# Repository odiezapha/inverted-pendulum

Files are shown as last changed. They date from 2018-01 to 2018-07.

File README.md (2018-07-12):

# Reaction Wheel Stabilized Inverted Pendulum
An inverted pendulum that maintains an upright attitude via reaction wheels. This repository
contains hardware and software development files. See the pdf for system equations.

Renderings:<br />
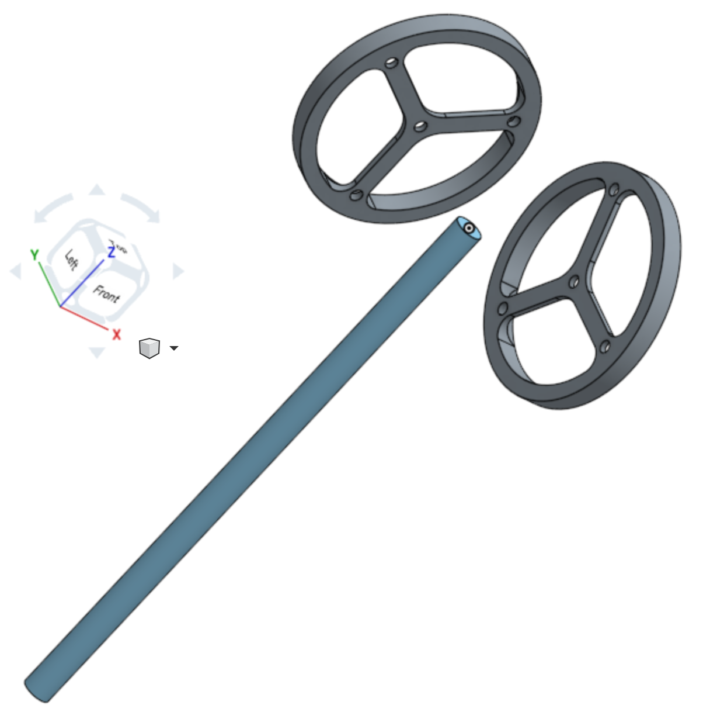
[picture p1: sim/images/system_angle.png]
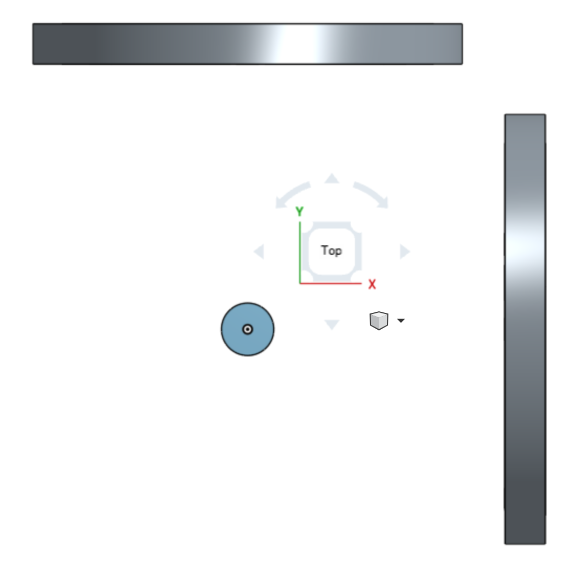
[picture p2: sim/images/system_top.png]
 

Simulation output:<br />
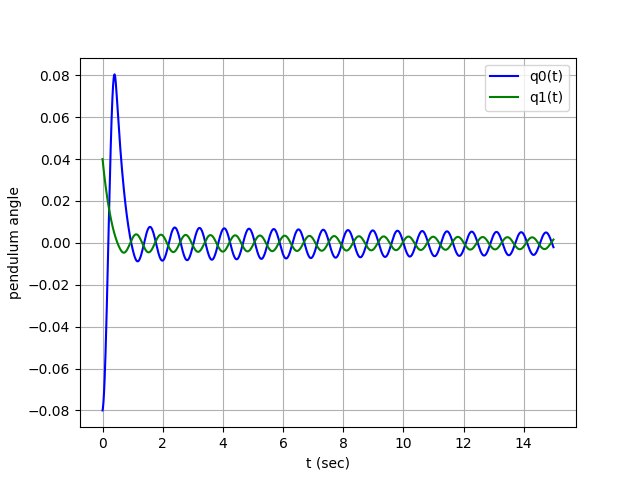
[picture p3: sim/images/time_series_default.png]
<br />
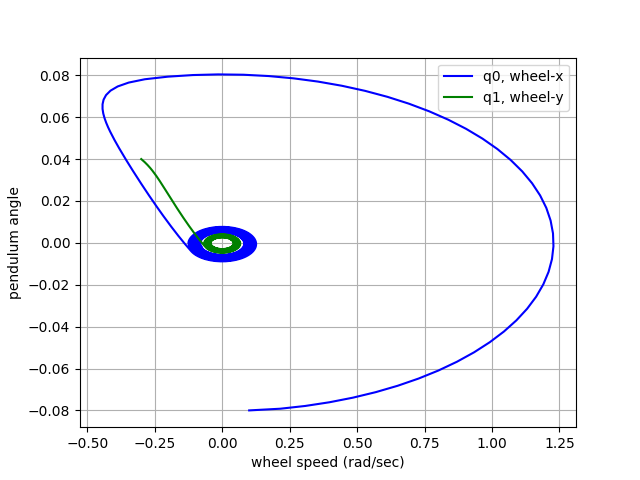
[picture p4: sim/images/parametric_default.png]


**Sim Test Conditions**<br />
Software: Python 3.6.4 on macOS High Sierra<br />
Computer: MacBook (Retina, 12-inch, Early 2015)<br />
Processor: 1.1 GHz Intel Core M<br />
RAM: 8 GB 1600 MHz DDR3<br />

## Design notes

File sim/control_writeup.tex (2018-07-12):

\documentclass{article}
\setlength{\parskip}{1em}
\usepackage{amsmath}
\usepackage{listings}
\usepackage{graphicx}
\graphicspath{ {./images/} }
\allowdisplaybreaks

\begin{document}

\centerline{\sc \large Reaction Wheel Stabilized Inverted Pendulum}
\vspace{.25pc}
\centerline{\sc \small optimal control, state space, and quaternions, oh my}
\vspace{.5pc}
\centerline{\sc Trent Fehl}
\vspace{1pc}

\begin{abstract}
In an attempt to develop some new skills, I started development of an 
inverted pendulum. This paper describes the system and the optimal 
controller development for the reaction wheel stabilized inverted pendulum.
Not included in this paper is the printed circuit board design, part 
selection, CAD models for the wheels, and machine paths for wheel manufacture.
I drew from papers concerning optimal control of a cart stabilized inverted 
pendulum, PID control of a reaction wheel stabilized inverted pendulum, 
and finally satellite control systems papers that utilize quaternions.
\end{abstract}

\section*{System Description}
\noindent This inverted pendulum is stabilized by the spinning of reaction wheels
mounted to the end of the pendulum. Only the case of a pendulum which is 
initiated and is controlled to its inverted position is being considered.
In addition to the wheels at the end of the pendulum rod, there is mass
associated with motors, a printed circuit board, batteries, and structure.
Theses are not shown in the image below but their masses are configurable 
variables for the control system.

\begin{figure}[h]
\centering
\begin{minipage}{.5\textwidth}
 \centering
 
 \caption{System rotated.}
\end{minipage}%
\begin{minipage}{.5\textwidth}
 \centering
 
 \caption{Top of system.}
\end{minipage}
\end{figure}

\noindent The equations of motion were determined and are described below.
These equations are used to build a state space representation
of the system. The state space representation takes the form 
$\boldsymbol{\dot{x}(t)} = \boldsymbol{A}\boldsymbol{x(t)} + 
\boldsymbol{B}\boldsymbol{u(t)}$ where $x(t)$ is the system state 
at time $t$, $u(t)$ is the input to the system at time $t$, and $A$ 
and $B$ are their respective coefficients. Below are the expanded 
matrices with our variables $\omega$, rotational speed for the 
respective axis and quaternions represented by $\boldsymbol{q} = q_0 + q_1\,i 
+ q_2\,j + q_3\,k$. $\boldsymbol{q}$ and $\boldsymbol{w}$ are measured 
by a 3-axis accelerometer and a 3-axis gyroscope, respectively.

\[
\begin{bmatrix}
\underset{3\times 1}{\boldsymbol{\dot{q}}} \\
\underset{3\times 1}{\boldsymbol{\dot{\omega}_p}} \\
\underset{3\times 1}{\boldsymbol{\dot{\omega}_w}}
\end{bmatrix}
=
\begin{bmatrix}
\underset{3\times 3}{\boldsymbol{0}} & \underset{3\times 3}{\boldsymbol{A_{12}}} & \underset{3\times 3}{\boldsymbol{0}} \\
\underset{3\times 3}{\boldsymbol{A_{21}}} & \underset{3\times 3}{\boldsymbol{A_{22}}} & \underset{3\times 3}{\boldsymbol{A_{23}}} \\
\underset{3\times 3}{\boldsymbol{0}} & \underset{3\times 3}{\boldsymbol{0}} & \underset{3\times 3}{\boldsymbol{A_{33}}}
\end{bmatrix}
\begin{bmatrix}
\underset{3\times 1}{\boldsymbol{q}} \\
\underset{3\times 1}{\boldsymbol{\omega_p}} \\
\underset{3\times 1}{\boldsymbol{\omega_w}}
\end{bmatrix}
+
\begin{bmatrix}
\underset{3\times 3}{\boldsymbol{0}} \\
\underset{3\times 3}{\boldsymbol{B_{21}}} \\
\underset{3\times 3}{\boldsymbol{B_{31}}}
\end{bmatrix}
\begin{bmatrix}
\underset{3\times 1}{\boldsymbol{\mu}}
\end{bmatrix}
\]

\noindent See \cite{mitstatespace} for more information about this representation.

\section*{\small Quaternion Equations}
\[
\begin{bmatrix}
\dot{q}_0 \\
\dot{q}_1 \\
\dot{q}_2 \\
\dot{q}_3
\end{bmatrix}
=
\frac{1}{2}
\begin{bmatrix}
q_0 & -q_1 & -q_2 & -q_3 \\
q_1 & q_0 & -q_3 & q_2 \\
q_2 & q_3 & q_0 & -q_1 \\
q_3 & -q_2 & q_1 & q_0 \\
\end{bmatrix}
\begin{bmatrix}
0 \\
\omega_1 \\
\omega_2 \\
\omega_3
\end{bmatrix}
\]

\noindent The above is apparently from \cite{noaccess} but I was not able to
get access to it. It makes sense though: The rate of change in
attitude should have the same units as angular speed times an
attitude. In the equation below we simply zero-out the $\dot{q}_0$
term and substitute in for $q_0$ using $q_0 = \sqrt{1 - q_1^2 
- q_2^2 - q_3^2}$. This reduces the number of terms in the equation
and per \cite{quatsforspacecraft} is still controllable.

\[
\begin{bmatrix}
\dot{q}_1 \\
\dot{q}_2 \\
\dot{q}_3
\end{bmatrix}
=
\frac{1}{2}
\begin{bmatrix}
\sqrt{1 - q_1^2 - q_2^2 - q_3^2} & -q_3 & q_2 \\
q_3 & \sqrt{1 - q_1^2 - q_2^2 - q_3^2} & -q_1 \\
-q_2 & q_1 & \sqrt{1 - q_1^2 - q_2^2 - q_3^2}
\end{bmatrix}
\begin{bmatrix}
\omega_1 \\
\omega_2 \\
\omega_3
\end{bmatrix}
\]

\noindent Finally we linearlize this using small angle approximation and the 
Taylor series expansion with the following equation. 

$$\boldsymbol{q} = \left[ q_0, q_1, q_2, q_3 \right]^T 
= \left[ \cos\frac{\theta}{2}, \boldsymbol{\hat{e}}^T\sin\frac{\theta}{2} \right]^T$$ 

\noindent We can do this if we assume the pendulum system is started in appoximately 
the upright position and maintains that attitude. The Taylor series expansion 
is then centered around $\theta = 0$, reducing the $\sin\frac{\theta}{2}$ terms to $0$.

\[
\begin{bmatrix}
\dot{q}_1 \\
\dot{q}_2 \\
\dot{q}_3
\end{bmatrix}
=
\frac{1}{2}
\begin{bmatrix}
1 & 0 & 0\\
0 & 1 & 0 \\
0 & 0 & 1
\end{bmatrix}
\begin{bmatrix}
\omega_1 \\
\omega_2 \\
\omega_3
\end{bmatrix}
\]

\section*{\small Angular Rotation Equations}
\noindent Again using the small angle approximation we can write the equation
of motion for the change in rotational speed in terms of quaterions.

$$\dot{\omega}_{px}\; =\;
\frac{-b_{wx}}{I_{px}}\,\omega_{wx}\;
+ \frac{b_{px}}{I_{px}}\,\omega_{px}\;
+ \frac{2glm}{I_{px}}\,q_1\;
+ \frac{k_s}{I_{px}}\,\mu$$

$$\dot{\omega}_{py}\; =\;
\frac{-b_{wy}}{I_{py}}\,\omega_{wy}\;
+ \frac{b_{py}}{I_{py}}\,\omega_{py}\;
+ \frac{2glm}{I_{py}}\,q_2\;
+ \frac{k_s}{I_{py}}\,\mu$$

\noindent The third equation does not have to be solved for basic operation because
we're not controlling around that axis. Below is what I think may work if 
a third wheel was added. $F_{spin}$ is a term that covers force of rotation around
the Z-axis while the pendulum is not vertical. We can simply set it equal
to 1 for this simulation.

$$\dot{\omega}_{pz}\; =\;
\frac{-b_{wy}}{I_{pz}}\,\omega_{wz}\;
+ \frac{b_{pz}}{I_{pz}}\,\omega_{pz}\;
+ \frac{2gF_{spin}}{I_{pz}}\,q_3\;
+ \frac{k_s}{I_{pz}}\,\mu$$

\noindent Working our way through the terms on the right side of the equal 
sign we have force from friction in the wheel bearings, force from friction
at the pendulum point of rotation, force of gravity pulling the pendulum 
down, and then finally the force of the wheels transferring momentum. The 
terms used are defined here:
\begin{itemize}
\setlength{\itemindent}{.5in}
\item $-b_w$ is the friction in the wheel bearings.
\item $\omega_w$ is rotational speed of the wheel.
\item $I_p$ is the moment of inertia of the pendulum system.
\item $b_p$ is the friction in the rotation of the pendulum rod.
\item $\omega_p$ is the rotational speed of the pendulum rod.
\item $g$ is gravitational acceleration (-9.81 $m/s^2$).
\item $l$ is the length of the pendulum rod.
\item $m$ is the combined mass at the end of the pendulum rod.
\item $k_s$ is the voltage applied to the motor.
\end{itemize}

\noindent Finally we have the equation for the rate of change of the 
reaction wheel rotational speed. There are two terms to account for 
here: friction in the wheel bearings and torque into the wheels from
the motor that we are controlling.

$$\dot{\omega}_{wx}\; =\;
\frac{-b_{wx}}{I_{wx}}\,\omega_{wx}\;
+ \frac{k_s}{I_{wx}}\,\mu$$

$$\dot{\omega}_{wy}\; =\;
\frac{-b_{wy}}{I_{wy}}\,\omega_{wy}\;
+ \frac{k_s}{I_{wy}}\,\mu$$

\noindent Where $I_w$ is the moment of inertia of the wheel.

\section*{\small Final State and Input Matrices}
Taking the equations from the previous two sections we can build
out the original state matrices.

$$\boldsymbol{A_{12}} = \frac{1}{2}\boldsymbol{I_3}$$

\begin{align*}
\boldsymbol{A_{21}} &=
\begin{bmatrix}
\frac{2glm}{I_{px}} & 0 & 0 \\[1em]
0 & \frac{2glm}{I_{py}} & 0 \\[1em]
0 & 0 & \frac{2gF_{spin}}{I_{pz}}
\end{bmatrix}
&
\boldsymbol{A_{22}} &=
\begin{bmatrix}
\frac{B_{px}}{I_{px}} & 0 & 0 \\[1em]
0 & \frac{B_{py}}{I_{py}} & 0 \\[1em]
0 & 0 & \frac{B_{pz}}{I_{pz}}
\end{bmatrix}\\[2em]
\boldsymbol{A_{23}} &=
\begin{bmatrix}
-\frac{B_{wx}}{I_{px}} & 0 & 0 \\[1em]
0 & -\frac{B_{wy}}{I_{py}} & 0 \\[1em]
0 & 0 & -\frac{B_{wz}}{I_{pz}}
\end{bmatrix}
&
\boldsymbol{A_{33}} &=
\begin{bmatrix}
-\frac{B_{wx}}{I_{wx}} & 0 & 0 \\[1em]
0 & -\frac{B_{wy}}{I_{wy}} & 0 \\[1em]
0 & 0 & -\frac{B_{wz}}{I_{wz}}
\end{bmatrix}\\[2em]
\boldsymbol{B_{21}} &=
\begin{bmatrix}
\frac{k_s}{I_{px}} & 0 & 0 \\[1em]
0 & \frac{k_s}{I_{py}} & 0 \\[1em]
0 & 0 & \frac{k_s}{I_{pz}}
\end{bmatrix}
&
\boldsymbol{B_{31}} &=
\begin{bmatrix}
\frac{k_s}{I_{wx}} & 0 & 0 \\[1em]
0 & \frac{k_s}{I_{wy}} & 0 \\[1em]
0 & 0 & \frac{k_s}{I_{wz}}
\end{bmatrix}\\
\end{align*}

\section*{Controller Development}
Here the controller design work will be described.

\section*{Software Operation}
The simulation software was developed on Mac OSX and Python 3.5.

\section*{\small Setup and Execution}
\noindent The user of this script should first set up a profile 
in the config files that represents the motors, pendulum, and 
wheels that they wish to simulate. They then need to update the 
three lines in pendulum.py where the config is chosen.

\begin{lstlisting}[language=python]
# Set configuration
motor = config_motor.maxon_70w
wheel = config_wheel.estimate
pend = config_pendulum.estimate
\end{lstlisting}

\noindent The script can then be invoked with:
\begin{lstlisting}[language=bash]
$ python pendulum.py
\end{lstlisting}

\section*{\small Output}
\noindent The output will provide the user with the K values and 
a plot of the simulated control given the initial gains and starting
position of the pendulum. Below is the output from a simulation using
the default initialization.

\begin{figure}
\centering

\end{figure}

\begin{figure}
\centering

\end{figure}

\begin{thebibliography}{9}
\bibitem{mitstatespace} 
State-Space Representation of LTI Systems, Derek Rowell October 2002
\\\texttt{http://web.mit.edu/2.14/www/Handouts/StateSpace.pdf}

\bibitem{quatsforspacecraft} 
Yaguang Yang,
\textit{Quaternion based model for momentum biased nadir pointing spacecraft}, 
Aerospace Science and Technology 14 (2010) 199–202

\bibitem{noaccess} 
B. Wie, 
\textit{Vehicle Dynamics and Control}, 
AIAA Education Series, AIAA, Reston, VA, 1998.
\end{thebibliography}

\end{document}

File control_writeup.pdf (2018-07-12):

Reaction Wheel Stabilized Inverted Pendulum

optimal control, state space, and quaternions, oh my

Trent Fehl

Abstract

In an attempt to develop some new skills, I started development of an inverted pendulum. This paper describes the system and the optimal controller development for the reaction wheel stabilized inverted pendulum. Not included in this paper is the printed circuit board design, part selection, CAD models for the wheels, and machine paths for wheel manufacture. I drew from papers concerning optimal control of a cart stabilized inverted pendulum, PID control of a reaction wheel stabilized inverted pendulum, and finally satellite control systems papers that utilize quaternions.

## System Description

This inverted pendulum is stabilized by the spinning of reaction wheels mounted to the end of the pendulum. Only the case of a pendulum which is initiated and is controlled to its inverted position is being considered. In addition to the wheels at the end of the pendulum rod, there is mass associated with motors, a printed circuit board, batteries, and structure. Theses are not shown in the image below but their masses are configurable variables for the control system.

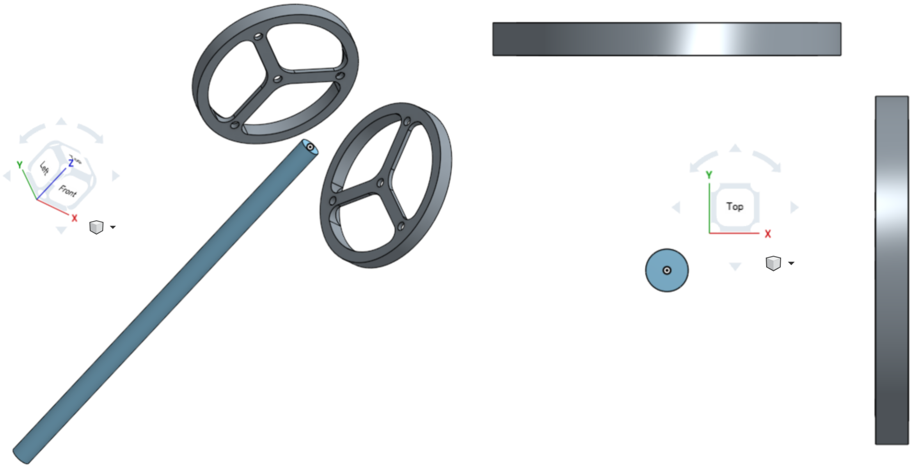
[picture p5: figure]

Figure 1: System rotated. | Figure 2: Top of system.

1

The equations of motion were determined and are described below. These equations are used to build a state space representation of the system. The state space representation takes the form x˙ (t) = Ax(t) + Bu(t) where x(t) is the system state at time t, u(t) is the input to the system at time t, and A and B are their respective coefficients. Below are the expanded matrices with our variables ω, rotational speed for the respective axis and quaternions represented by q = q0 + q1 i + q2 j + q3 k. q and w are measured by a 3-axis accelerometer and a 3-axis gyroscope, respectively.

q˙
3×1
ω˙ p

3×1
ω˙ w
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
See [1] for more information about this representation.

Quaternion Equations

q˙0
q˙1
q˙2
q˙3

=

1
2

q0 | −q1 | −q2 | −q3
q1 | q0 | −q3 | q2
q2 | q3 | q0 | −q1
q3 | −q2 | q1 | q0

0
ω1
ω2
ω3

The above is apparently from [3] but I was not able to get access to it. It makes sense though: The rate of change in attitude should have the same units as angular speed times an attitude. In the equation below we simply zero-out the q˙0 term and substitute in for q0 using q0 =

p
1 − q

2
1 − q

2
2 − q
2/3. This reduces the
number of terms in the equation and per [2] is still controllable.

q˙1
q˙2
q˙3
- =

1
2

p
1 − q

2
1 − q

2
2 − q

2
3 | −q3 | q2
q3

p
1 − q
| 2 1 − q

2
2 − q

2
3 | −q1
−q2 | q1

p
1 − q
| | 2 1 − q

2
2 − q

2
3

ω1
ω2
ω3

Finally we linearlize this using small angle approximation and the Taylor series expansion with the following equation.

q = [q0, q1, q2, q3]

T =

cos

θ
2

, eˆ

T
sin

θ
2

T

2

We can do this if we assume the pendulum system is started in appoximately the upright position and maintains that attitude. The Taylor series expansion is then centered around θ = 0, reducing the sin θ
2

terms to 0.

q˙1
q˙2
q˙3
- =

1
2

1 0 0
0 1 0
0 0 1

ω1
ω2
ω3

Angular Rotation Equations

Again using the small angle approximation we can write the equation of motion for the change in rotational speed in terms of quaterions.

ω˙ px =

−bwx

Ipx

ωwx +

bpx

Ipx

ωpx +

2glm

Ipx

q1 +

ks

Ipx

µ

ω˙ py =

−bwy
Ipy

ωwy +

bpy
Ipy

ωpy +

2glm
Ipy

q2 +

ks
Ipy

µ

The third equation does not have to be solved for basic operation because we’re not controlling around that axis. Below is what I think may work if a third wheel was added. Fspin is a term that covers force of rotation around the Z-axis while the pendulum is not vertical. We can simply set it equal to 1 for this simulation.

ω˙ pz =

−bwy

Ipz

ωwz +

bpz

Ipz

ωpz +

2gFspin

Ipz

q3 +

ks

Ipz

µ

Working our way through the terms on the right side of the equal sign we have force from friction in the wheel bearings, force from friction at the pendulum point of rotation, force of gravity pulling the pendulum down, and then finally the force of the wheels transferring momentum. The terms used are defined here:

- −bw is the friction in the wheel bearings.
- ωw is rotational speed of the wheel.
- Ip is the moment of inertia of the pendulum system.
- bp is the friction in the rotation of the pendulum rod.

3

- ωp is the rotational speed of the pendulum rod.
- g is gravitational acceleration (-9.81 m/s²
).
- l is the length of the pendulum rod.
- m is the combined mass at the end of the pendulum rod.
- ks is the voltage applied to the motor.

Finally we have the equation for the rate of change of the reaction wheel rotational speed. There are two terms to account for here: friction in the wheel bearings and torque into the wheels from the motor that we are controlling.

ω˙ wx =

−bwx

Iwx

ωwx +

ks

Iwx

µ

ω˙ wy =

−bwy
Iwy

ωwy +

ks
Iwy

µ

Where Iw is the moment of inertia of the wheel.

Final State and Input Matrices

Taking the equations from the previous two sections we can build out the original state matrices.

A12 =

1
2

I3

A21 =

2glm

Ipx

0 | 0

0

2glm Ipy | 0
0 | 0 | 2gFspin
| | Ipz

A22 =

Bpx

Ipx

| 0 | 0
0 | Bpy Ipy | 0
0 | 0 | Bpz Ipz

A23 =

−

Bwx
Ipx
0 | 0
0 | −

Bwy

Ipy

0

0 | 0 | −

Bwz
Ipz

A33 =

−

Bwx
Iwx
0 | 0
0 | −

Bwy

Iwy

0

0 | 0 | −

Bwz
Iwz

4

B21 =

ks
Ipx

0 0

0

ks
Ipy

0

0 | 0 | ks
Ipz

B31 =

ks
Iwx

0 0

0

ks
Iwy

0

0 | 0 | ks
Iwz

## Controller Development

Here the controller design work will be described.

## Software Operation

The simulation software was developed on Mac OSX and Python 3.5.

Setup and Execution

The user of this script should first set up a profile in the config files that repre-sents the motors, pendulum, and wheels that they wish to simulate. They then need to update the three lines in pendulum.py where the config is chosen.

# Se t c o n f i g u r a t i o n

motor = c o n fi g m o t o r . maxon 70w
wheel = c o n f i g w h e e l . e s tim a t e
pend = c on fi g pendulum . e s tim a t e

The script can then be invoked with:

$ python pendulum . py

Output

The output will provide the user with the K values and a plot of the simulated control given the initial gains and starting position of the pendulum. Below is the output from a simulation using the default initialization.

5

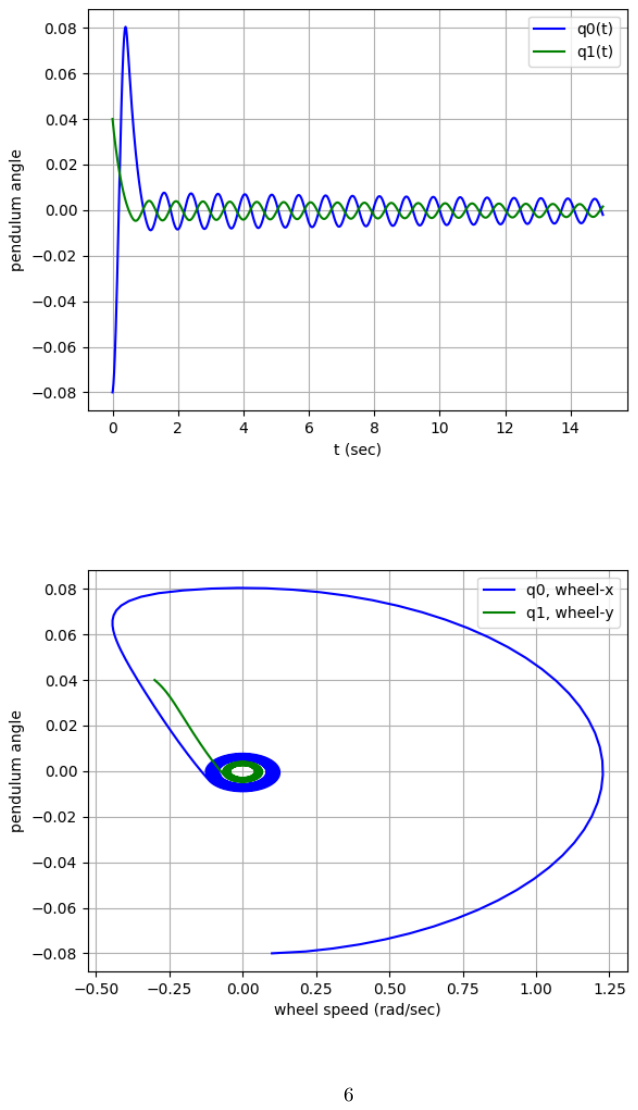
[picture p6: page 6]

6

## References

[1] State-Space Representation of LTI Systems, Derek Rowell October 2002 http://web.mit.edu/2.14/www/Handouts/StateSpace.pdf
[2] Yaguang Yang, Quaternion based model for momentum biased nadir pointing spacecraft, Aerospace Science and Technology 14 (2010) 199–202
[3] B. Wie, Vehicle Dynamics and Control, AIAA Education Series, AIAA, Reston, VA, 1998.

7

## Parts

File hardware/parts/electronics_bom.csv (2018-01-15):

type | part | manufacturer | voltage (min-max) | price per unit | number of units | price | datasheet
motor | 397172 | Maxon | 24 |  | 2 |  | https://www.maxonmotorusa.com/medias/sys_master/root/8825435127838/17-EN-267.pdf
motor driver | L6235 | ST Micro | 8-52 |  | 2 |  | http://www.st.com/content/ccc/resource/technical/document/datasheet/e0/55/d7/b1/d5/06/47/96/CD00002347.pdf/files/CD00002347.pdf/jcr:content/translations/en.CD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
microcontroller | STM32F401CEU | ST Micro | 1.7-3.6 |  |  |  | http://www.st.com/content/ccc/resource/technical/document/datasheet/b3/a5/46/3b/b4/e5/4c/85/DM00115249.pdf/files/DM00115249.pdf/jcr:content/translations/en.DM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
 |  |  |  |  |  |  | http://www.st.com/content/ccc/resource/technical/document/application_note/b9/9b/16/3a/12/1e/40/0c/CD00167594.pdf/files/CD00167594.pdf/jcr:content/translation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
boost converter | TPS61175 | Texas Instruments | 2.9-18 |  | 2 |  | http://www.ti.com/lit/ds/slvs892d/slvs892d.pdf
 |  |  |  |  |  |  | http://www.ti.com/lit/an/slva337/slva337.pdf
bms | AD7280A | Analog Devices | 8-30 |  |  |  | http://www.analog.com/media/en/technical-documentation/data-sheets/AD7280A.pdf
 |  |  |  |  |  |  | http://www.analog.com/media/en/technical-documentation/user-guides/UG-252.pdf
 |  |  |  |  |  |  | http://www.analog.com/media/en/reference-design-documentation/reference-designs/CN0235.pdf
accel | LIS3DE | ST Micro | 1.7-3.6 |  |  |  | http://www.st.com/content/ccc/resource/technical/document/datasheet/group3/10/aa/64/5a/f1/cc/49/7f/DM00066267/files/DM00066267.pdf/jcr:content/translations/en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
gyro | L3GD20H | ST Micro | 2.2-3.6 |  |  |  | http://www.st.com/content/ccc/resource/technical/document/datasheet/35/b1/e0/39/71/57/43/01/DM00060659.pdf/files/DM00060659.pdf/jcr:content/translations/en.DM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
battery | INR18650-25R5 | Samsung |  |  | 4 |  | https://www.powerstream.com/p/INR18650-25R-datasheet.pdf
battery charger | ISL9238 | Intersil | 3.2-23.4 |  |  |  | https://www.intersil.com/content/dam/Intersil/documents/isl9/isl9238-38a.pdf
 |  |  |  |  |  |  | https://www.intersil.com/content/dam/Intersil/documents/isl9/isl9238eval1z-user-guide.pdf
linear regulator | LM317 | Texas Instruments | X-20 |  |  |  | http://www.ti.com/lit/ds/symlink/lm317.pdf
USB connector | DX07S024JJ2R1300 | JAE Electronics |  |  |  |  | https://www.digikey.com/product-detail/en/jae-electronics/DX07S024JJ2R1300/670-2794-6-ND/5246069
current sense | LTC6102 | Linear Tech |  |  |  |  | http://cds.linear.com/docs/en/datasheet/6102fe.pdf
battery connector | 2-pin Female | XT60 |  |  |  |  | https://www.sparkfun.com/products/10474
battery holder
USB to UART | FT231X | FTDI |  |  |  |  | http://www.ftdichip.com/Support/Documents/DataSheets/ICs/DS_FT231X.pdf
USB controller | TUSB320LAI | Texas Instruments |  |  |  |  | http://www.ti.com/lit/ds/symlink/tusb320lai.pdf
thermistor | AT-4 Shape 1 | Semitec |  |  |  |  | http://www.mouser.com/ds/2/362/semitec_atthermistor-371460.pdf
inductor (charger) | WE-SD Rod Core Choke | Worth Electronik |  |  |  |  | http://katalog.we-online.de/pbs/datasheet/744710215.pdf
power transistor | EPC2023 | EPC |  |  |  |  | http://epc-co.com/epc/Portals/0/epc/documents/datasheets/EPC2023_datasheet.pdf
op amp | LM358 | ST Micro |  |  |  |  | http://static6.arrow.com/aropdfconversion/f8d16131022a36887086d0d189a6ab5e153d6d83/556438431794685cd000.pdf
inductor (converter) | MSS1038-153ML | Coilcraft |  |  |  |  | http://www.mouser.com/ds/2/597/mss1038-270676.pdf
schottky diode | SS3P6L | Vishay |  |  |  |  | https://www.vishay.com/docs/88987/ss3p6l.pdf
PCB motor connector | 39281083 | Molex |  |  |  |  | http://www.molex.com/pdm_docs/sd/039281083_sd.pdf
motor cable | 451350801 | Molex |  |  |  |  | http://www.literature.molex.com/SQLImages/kelmscott/Molex/PDF_Images/987651-5853.PDF
push button | ITS13FV2SR | C&K Components |  |  |  |  | http://www.ckswitches.com/media/1894/its.pdf
RGB LED | QBLP677-RGB (High Bright) | QT Brightek |  |  |  |  | http://www.qt-brightek.com/datasheet/QBLP677-RGB%20(High%20Bright).pdf
diode | BAT54C | Diodes Inc |  |  |  |  | https://www.diodes.com/assets/Datasheets/ds11005.pdf
p-channel fet | SI7655DN | Vishay |  |  |  |  | http://www.vishay.com/docs/63617/si7655dn.pdf
SPDT switch | Surface Mount Right Angle Switch | Sparkfun |  |  |  |  | https://www.sparkfun.com/products/597
mosfet | 2N7002 | Diodes Inc |  |  |  |  | https://www.diodes.com/assets/Datasheets/ds11303.pdf
crystal | ABM3B-16.000MHZ-B2-T

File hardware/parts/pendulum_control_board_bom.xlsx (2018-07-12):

Table 1
Item | Quantity Per PCB | Placement | Manufacturer PN | Manufacturer | Supplier PN | Supplier | Unit Price | Footprint | Value | References
1 | 34 | Do Not Place | CGA3E2X7R1E104K080AA | TDK Corporation | 445-5667-1-ND | digikey | 0.063 | 603 | 0.1uF | C1 C4 C5 C7 C8 C10 C11 C12 C13 C14 C15 C16 C18 C19 C20 C21 C22 C23 C25 C26 C37 C41 C43 C47 C56 C64 C65 C66 C71 C72 C74 C75 C79 C82
2 | 18 | Do Not Place | TMK107BJ105KA-T | Taiyo Yuden | 587-1248-1-ND | digikey | 0.06 | 603 | 1.0uF | C2 C17 C24 C49 C53 C57 C58 C59 C60 C61 C62 C63 C67 C68 C69 C70 C73 C76
3 | 4 | Do Not Place | GRM31CD80J107ME39L | Murata Electronics North America | 490-10525-1-ND | digikey | 0.57 | 1206 | 100uF | C36 C39 C42 C45
4 | 7 | Do Not Place | C0603C103J3GACTU | KEMET | 399-7838-1-ND | digikey | 0.33 | 603 | 10nF | C3 C6 C9 C28 C31 C32 C35
5 | 1 | Do Not Place | C0805C103J3GACTU | KEMET | 399-7990-1-ND | digikey | 0.034 | 805 | 10uF | C27
6 | 1 | Do Not Place | 1210D103J250KHT | Knowles Novacap | 1763-1060-1-ND | digikey | 4.91 | 1210 | 10uF | C77
7 | 2 | Do Not Place | C0603C102F3GACTU | KEMET | 399-7825-1-ND | digikey | 0.29 | 603 | 1nF | C29 C33
8 | 1 | Do Not Place | EMK107BJ225KA-T | Taiyo Yuden | 587-1430-1-ND | digikey | 0.12 | 603 | 2.2uF | C78
9 | 2 | Do Not Place | CL10B333KA8NNNC | Samsung Electro-Mechanics | 1276-2038-1-ND | digikey | 0.1 | 603 | 33nF | C30 C34 C40 C46
10 | 2 | Do Not Place | C0603C479D3GAC7867 | KEMET | 399-15411-1-ND | digikey | 0.29 | 603 | 4.7pF | C80 C81
11 | 4 | Do Not Place | C0603C472F3GACTU | KEMET | 399-9087-1-ND | digikey | 1.15 | 603 | 4.7uF | C48 C51 C52 C55
12 | 2 | Do Not Place | CL10B473KA8NFNC | Samsung Electro-Mechanics | 1276-2072-1-ND | digikey | 0.1 | 603 | 47nF | C50 C54
13 | 2 | Do Not Place | C0603C562K3RAC7867 | KEMET | 399-15415-6-ND | digikey | 0.29 | 603 | 5.6nF | C38 C44
14 | 4 | Do Not Place | DZ2J150M0L | Panasonic Electronics Components | DZ2J150M0LCT-ND | digikey | 0.21 | SMINI2-F5-B | 15V | D7 D8 D9 D10
15 | 4 | Do Not Place | 1N4148W-7-F | Diodes Incorporated | 1N4148W-FDICT-ND | digikey | 0.18 | SOD-123 | 1N4148 | D11 D12 D13 D14
16 | 3 | Do Not Place | 5973311402NF | Dialight | 350-3771-ND | digikey | 0.82 | 1206 | 5973311402 | D3 D4 D16
17 | 1 | Do Not Place | BAT54C RFG | Taiwan Semiconductor Corporation | BAT54CRFGCT-ND | digikey | 0.25 | DIODE_SOT23 | BAT54C | D2
18 | 2 | Do Not Place | MBR0520-TP | Micro Commercial Co | MBR0520TPMSCT-ND | digikey | 0.41 | SOD-123 | MBR0520 | D1 D17
19 | 1 | Do Not Place | QBLP677-RGB (HIGH BRIGHT) | QT Brighttek QTB | 1516-1195-1-ND | digikey | 0.89 | 4-PLCC | QBLP677-RGB | D15
20 | 2 | Do Not Place | LTST-C191KSKT | Lite-On Inc | 160-1448-1-ND | digikey | 0.31 | 603 | Yellow | D5 D6
21 | 3 | Do Not Place | 742792651 | Wurth Electronics Inc | 732-1593-1-ND | digikey | 0.17 | 603 | 30~/1.8A | FB1 FB2 FB3
22 | 1 | Place | LM358DT | STMicroelectronics | 497-1591-1-ND | digikey | 0.43 | SO08 | LM358D | IC2
23 | 1 | Place | STM32F401CBU6 | STMicroelectronics | 497-17425-ND | digikey | 4.98 | UFQFPN48 | STM32F411CEU6 | IC1
24 | 1 | Place | DX07S024JJ2R1300 | JAE Electronics | 670-2794-1-ND | digikey | 2.61 |  | DX07S024JJ2 | J1
25 | 2 | Do Not Place | MSS1038-153MLC | Coilcraft | 994-MSS1038-153MLC | mouser | 1.73 | INDUCTOR-COILCRAFT_MSS1038 | MSS1038-153ML | L1 L2
26 | 3 | Do Not Place | 2N7002H-7 | Diodes Incorporated | 2N7002H-7DICT-ND | digikey | 0.3 | SOT23 | 2N7002 | Q5 Q6 Q7
27 | 4 | Do Not Place | BSS138P,215 | Nexperia USA Inc. | 1727-1142-1-ND | digikey | 0.28 | SOT23 | BSS138 | Q1 Q2 Q3 Q4
28 | 3 | Do Not Place | RC0603JR-070RL | Yageo | 311-0.0GRCT-ND | digikey | 0.1 | 603 | 0 | R83 R103 R104
29 | 1 | Do Not Place | PMR03EZPFU10L0 | Rohm Semiconductor | RHM0.01BVCT-ND | digikey | 0.69 | 603 | 0.01 | R88
30 | 1 | Do Not Place | WSL0603R0200FEA | Vishay Dale | WSLJ-.02CT-ND | digikey | 0.84 | 603 | 0.02 | R80
31 | 2 | Do Not Place | UCR03EWPFSR030 | Rohm Semiconductor | RHM1268CT-ND | digikey | 0.58 | 603 | 0.3 | R45 R58
32 | 4 | Do Not Place | ERJ-3RQF1R0V | Panasonic Electronics Components | P1.0AJCT-ND | digikey | 0.17 | 603 | 1 | R81 R82 R86 R87
33 | 3 | Do Not Place | MCT06030C1801FP500 | Vishay Beyschlag | MCT0603-1.80K-CFCT-ND | digikey | 0.18 | 603 | 1.8K | R42 R55 R61
34 | 2 | Do Not Place | ERA-3AEB101V | Panasonic Electronics Components | P100DBCT-ND | digikey | 0.35 | 603 | 100 | R41 R54
35 | 7 | Do Not Place | RT0603BRD07100KL | Yageo | YAG1235CT-ND | digikey | 0.35 | 603 | 100K | R44 R57 R93 R94 R95 R96 R105
36 | 20 | Do Not Place | MCT06030C1002FP500 | Vishay Beyschlag | MCT0603-10.0K-CFCT-ND | digikey | 0.152 | 603 | 10K | R10 R15 R17 R21 R25 R27 R28 R29 R30 R31 R34 R35 R38 R48 R66 R76 R89 R91 R102 R106
37 | 1 | Do Not Place | ERA-3AEB1073V | Panasonic Electronics Components | P107KDBCT-ND | digikey | 0.35 | 603 | 107K | R79
38 | 1 | Do Not Place | ERA-3AEB1153V | Panasonic Electronics Components | P115KDBCT-ND | digikey | 0.35 | 603 | 115K | R85
39 | 1 | Do Not Place | ERA-3AEB1400V | Panasonic Electronics Components | P140DBCT-ND | digikey | 0.35 | 603 | 140 | R72
40 | 2 | Do Not Place | ERA-3AEB1873V | Panasonic Electronics Components | P187KDBCT-ND | digikey | 0.35 | 603 | 187K | R47 R65
41 | 9 | Do Not Place | ERA-3AEB102V | Panasonic Electronics Components | P1.0KDBCT-ND | digikey | 0.35 | 603 | 1K | R32 R33 R36 R37 R51 R59 R64 R67 R70
42 | 1 | Do Not Place | CSR1206-0R001F1 | Riedon | 696-1369-1-ND | digikey | 0.59 | 1206 | 1m | R99
43 | 2 | Do Not Place | CPF0603B1M0E | TE Connectivity Passive Product | A119955CT-ND | digikey | 0.52 | 603 | 1M | R49 R62
44 | 1 | Do Not Place | ERA-3AEB202V | Panasonic Electronics Components | P2.0KDBCT-ND | digikey | 0.35 | 603 | 2K | R84
45 | 1 | Do Not Place | ESR03EZPJ200 | Rohm Semiconductor | RHM20DCT-ND | digikey | 0.1 | 603 | 20 | R98
46 | 2 | Do Not Place | ERA-3AEB204V | Panasonic Electronics Components | P200KDBCT-ND | digikey | 0.35 | 603 | 200K | R3 R4
47 | 3 | Do Not Place | ESR03EZPJ221 | Rohm Semiconductor | RHM220DCT-ND | digikey | 0.1 | 603 | 220 | R77 R90 R92
48 | 1 | Do Not Place | RC0603FR-07330RL | Yageo | 311-330HRCT-ND | digikey | 0.1 | 603 | 330 | R97
49 | 2 | Do Not Place | ERA-3AEB333V | Panasonic Electronics Components | P33KDBCT-ND | digikey | 0.35 | 603 | 33K | R40 R53
50 | 3 | Do Not Place | ERA-3AEB302V | Panasonic Electronics Components | P3.0KDBCT-ND | digikey | 0.35 | 603 | 3K | R69 R71 R73
51 | 1 | Do Not Place | ERA-3AEB4531V | Panasonic Electronics Components | P4.53KDBCT-ND | digikey | 0.35 | 603 | 4.5K | R74
52 | 1 | Do Not Place | RNCP0603FTD4R70 | Stackpole Electronics Inc | RNCP0603FTD4R70CT-ND | digikey | 0.1 | 603 | 4.7 | R75
53 | 6 | Do Not Place | ERA-3AEB472V | Panasonic Electronics Components | P4.7KDBCT-ND | digikey | 0.35 | 603 | 4.7K | R2 R5 R6 R9 R50 R63
54 | 1 | Do Not Place | RC0603FR-07402KL | Yageo | 311-402KHRCT-ND | digikey | 0.1 | 603 | 402K | R78
55 | 2 | Do Not Place | MCT06030C4700FP500 | Vishay Beyschlag | MCT0603-470-CFCT-ND | digikey | 0.18 | 603 | 470 | R7 R8
56 | 2 | Do Not Place | ERA-3AEB473V | Panasonic Electronics Components | P47KDBCT-ND | digikey | 0.35 | 603 | 47K | R39 R52
57 | 2 | Do Not Place | ESR03EZPJ562 | Rohm Semiconductor | RHM5.6KDCT-ND | digikey | 0.1 | 603 | 5.6K | R43 R56
58 | 8 | Do Not Place | ESR03EZPJ680 | Rohm Semiconductor | RHM68DCT-ND | digikey | 0.1 | 603 | 68 | R11 R12 R13 R14 R19 R20 R23 R24
59 | 2 | Do Not Place | RC0603FR-0780R6L | Yageo | 311-80.6HRCT-ND | digikey | 0.1 | 603 | 80 | R60 R68
60 | 1 | Do Not Place | RC0603FR-07909KL | Yageo | 311-909KHRCT-ND | digikey | 0.1 | 603 | 900K | R1
61 | 7 | Do Not Place | Resistor (DNP) |  | DNP |  |  | 603 | DNP | R16 R18 R22 R26 R46 R100 R101
62 | 1 | Do Not Place | RS-187R05A2-DS MT RT (DNP) | C&K | CKN10361CT-ND | digikey | 0.53 | SW-SPST | DNP | S3
63 | 2 | Do Not Place | CUS-12TB (DNP) | Nidec Copal Electronics | 563-1102-1-ND | digikey | 0.71 | Surface Mount, Right Angle | DNP | S1 S2
64 | 1 | Place | AD7280AWBSTZ | Analog Devices Inc | AD7280AWBSTZ-ND | digikey | 10.65 | LQFP48_N | AD7280A | U$5
65 | 4 | Place | EPC2023 | EPC | 917-1088-1-ND | digikey | 8.21 | EPC2023 | EPC2023 | U$14 U$15 U$16 U$17
66 | 1 | Place | FT231XS-R | FTDI | 768-1129-1-ND | digikey | 2.12 | SSOP20_L | FT231XS | U1
67 | 1 | Place | ISL9238HRTZ-T7A | Intersil | ISL9238HRTZ-T7ACT-ND | digikey | 8.78 | TQFN-32 | ISL9238 | U$10
68 | 1 | Place | ITS13FV2SR | C&K | CKN10459CT-ND | digikey | 4.58 | ITS13FV2SR | ITS13FV2SR | U$8
69 | 1 | Place | L3GD20HTR | STMicroelectronics | 497-13931-1-ND | digikey | 3.42 | LGA-16 | L3GD20H | U$4
70 | 2 | Place | L6235D013TR | STMicroelectronics | 497-4009-1-ND | digikey | 7.33 | SO24W | L6235 | U$1 U$7
71 | 1 | Place | LIS3DETR | STMicroelectronics | 497-16262-1-ND | digikey | 1.36 | LGA-16 | LIS3DE | U$3
72 | 1 | Place | LTC6102IDD#PBF | Linear Technology/Analog devices | LTC6102IDD#PBF-ND | digikey | 4.07 | DFN8-3X3 | LTC6102DD | U5
73 | 1 | Place | SI7655DN-T1-GE3 | Vishay/Siliconix | 78-SI7655DN-T1-GE3 | mouser | 1.65 | POWERPAK-1212-8S | SI7655DN | U$18
74 | 2 | Place | SS5P6-M3/86A | Vishay Semiconductor Diodes | SS5P6-M3/86AGICT-ND | digikey | 0.65 | TO-277A | SS3P6L | U$9 U$13
75 | 2 | Place | TPS61175PWPR | Texas Instruments | 296-24013-1-ND | digikey | 3.12 | HTSSOP14PWP | TPS61175 | U$2 U$11
76 | 1 | Place | TUSB320LAIRWBR | Texas Instruments | 595-TUSB320LAIRWBR | digikey | 1.82 | X2QFN-12 | TUSB320LAI | U$6
77 | 2 | Do Not Place | MIC5201-5.0YS | Microchip Technology | 576-1254-ND | digikey | 1.4 | SOT223 | V_REG_317SMD | U2 U3
78 | 1 | Do Not Place | 744710215 (DNP) | Wurth Electronics Inc | 732-3252-ND | digikey | 1.9 | ROD-CORE-CHOKE | DNP | U$12
79 | 2 | Do Not Place | 39281083 (DNP) | Molex LLC | WM3803-ND | digikey | 1.3 | CON-MOLEX_5566-8 | DNP | X1 X2
80 | 1 | Do Not Place | ST3215SB32768E0HPWBB | AVX Corp/Kyocera Corp | 1253-1335-1-ND | digikey | 0.66 | CRYSTAL-SMD-3.2X1.5MM | 32.768kHz | Y2

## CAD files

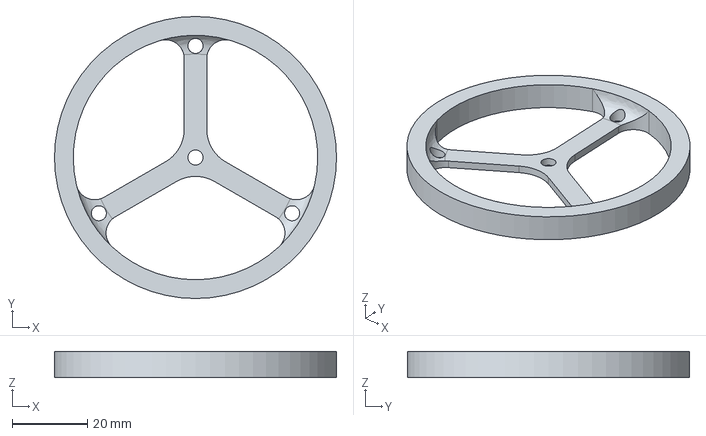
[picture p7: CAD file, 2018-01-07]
hardware/parts/cad/wheel.step
75.0 x 75.0 x 7.00 mm

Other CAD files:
hardware/parts/cad/wheel.fcstd

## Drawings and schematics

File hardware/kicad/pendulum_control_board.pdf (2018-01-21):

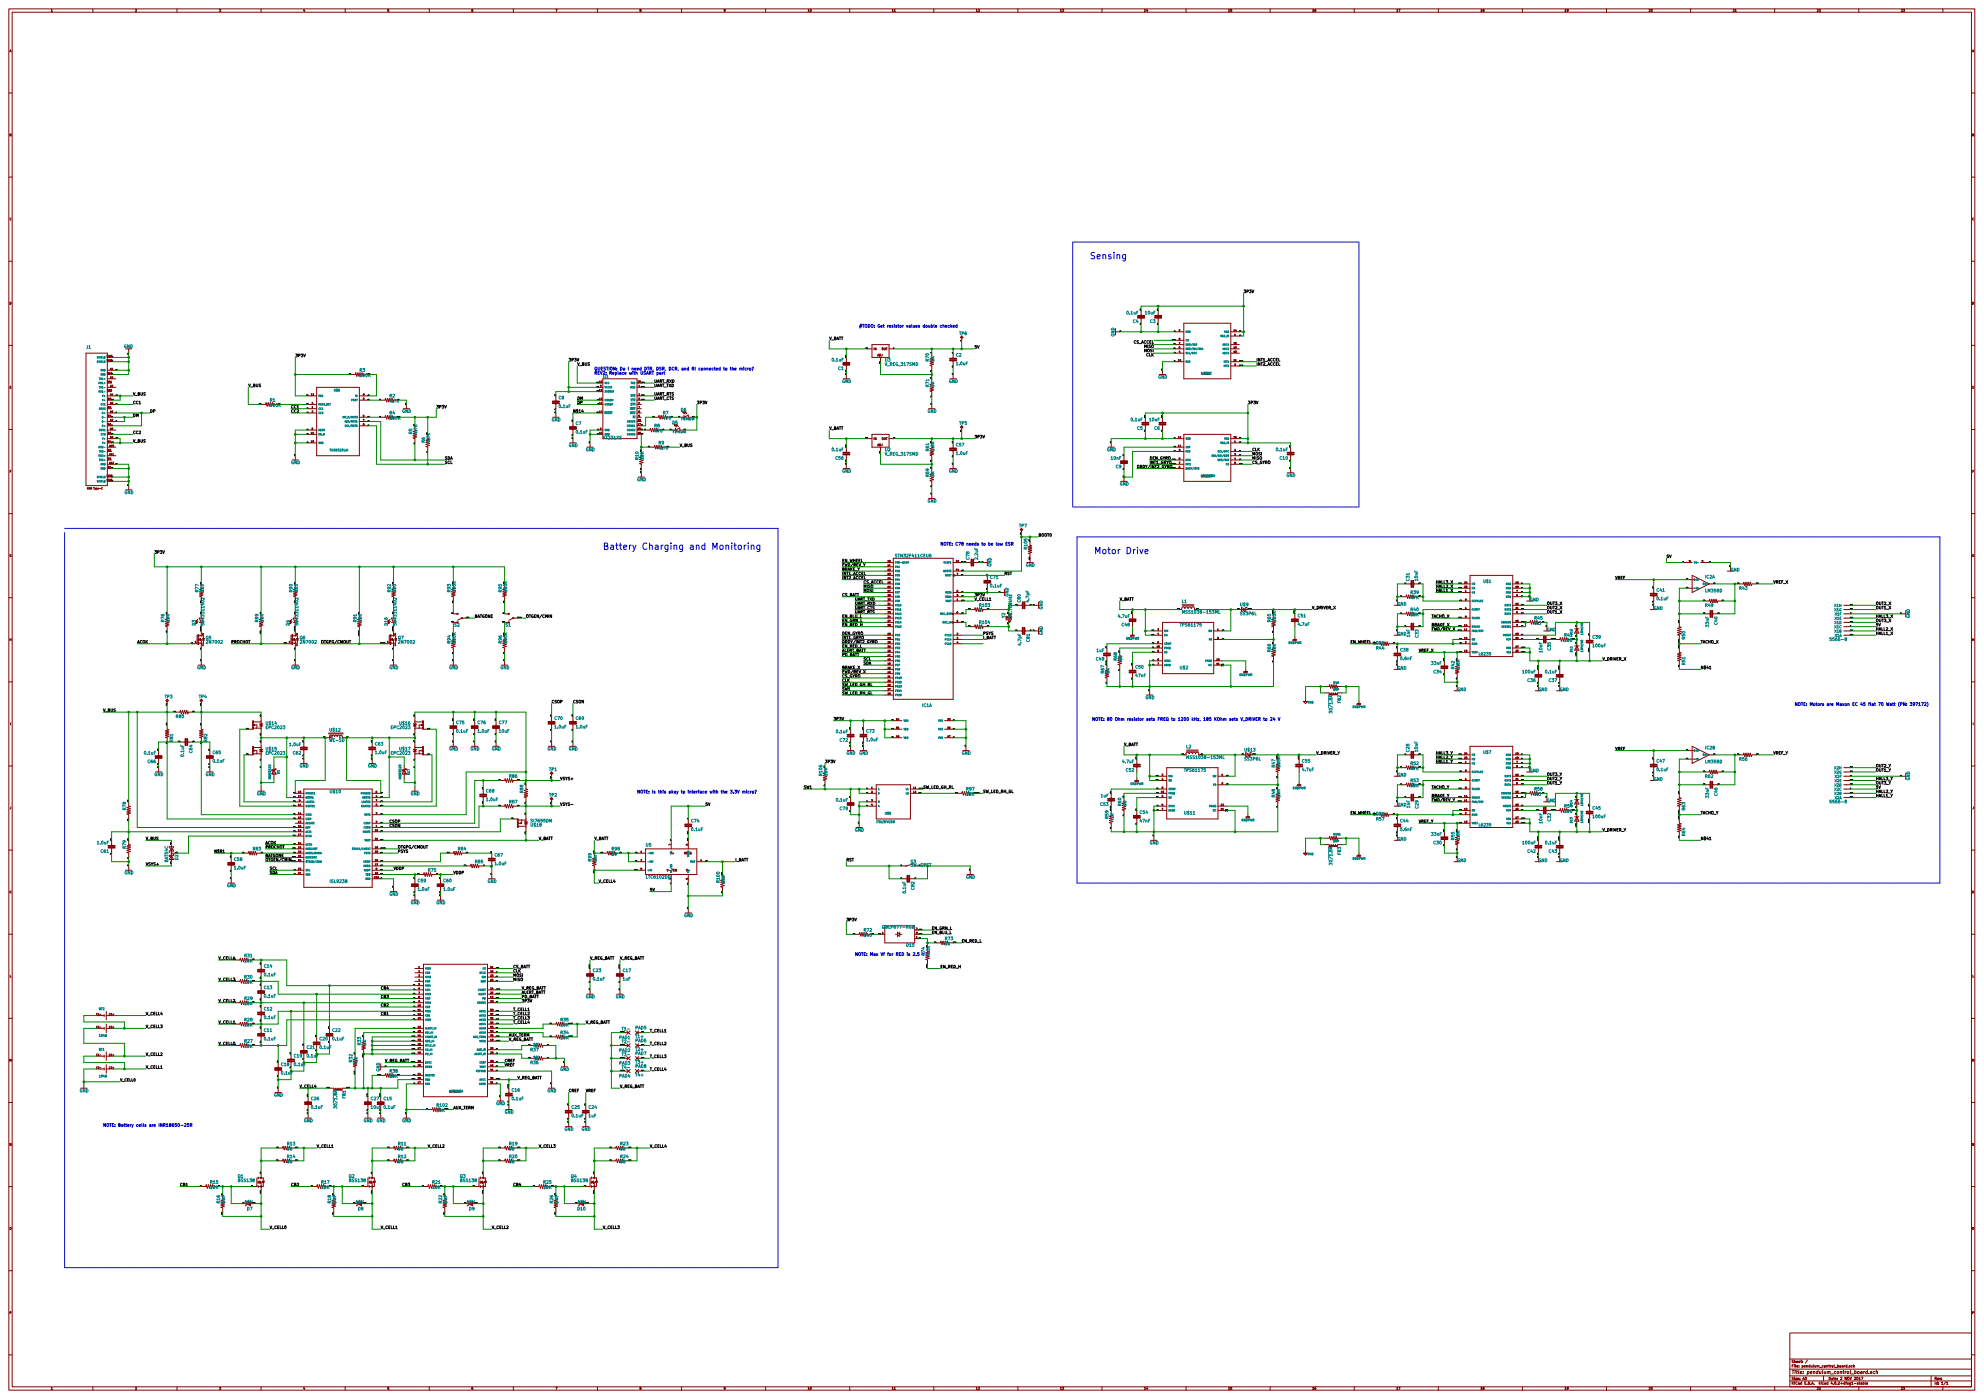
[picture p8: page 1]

#TODO: Get resistor values double checked

QUESTION: Do I need DTR, DSR, DCR, and RI connected to the micro?
REV2: Replace with USART part

GND GND GNDGND GND GND GND

Motor Drive Battery Charging and Monitoring

NOTE: C78 needs to be low ESR

NOTE: Motors are Maxon EC 45 flat 70 Watt (PN: 397172)

NOTE: 80 Ohm resistor sets FREQ to 1200 kHz, 185 KOhm sets V_DRIVER to 24 V

NOTE: Is this okay to interface with the 3.3V micro?

NOTE: Max Vf for RED is 2.5 V

NOTE: Battery cells are INR18650-25R

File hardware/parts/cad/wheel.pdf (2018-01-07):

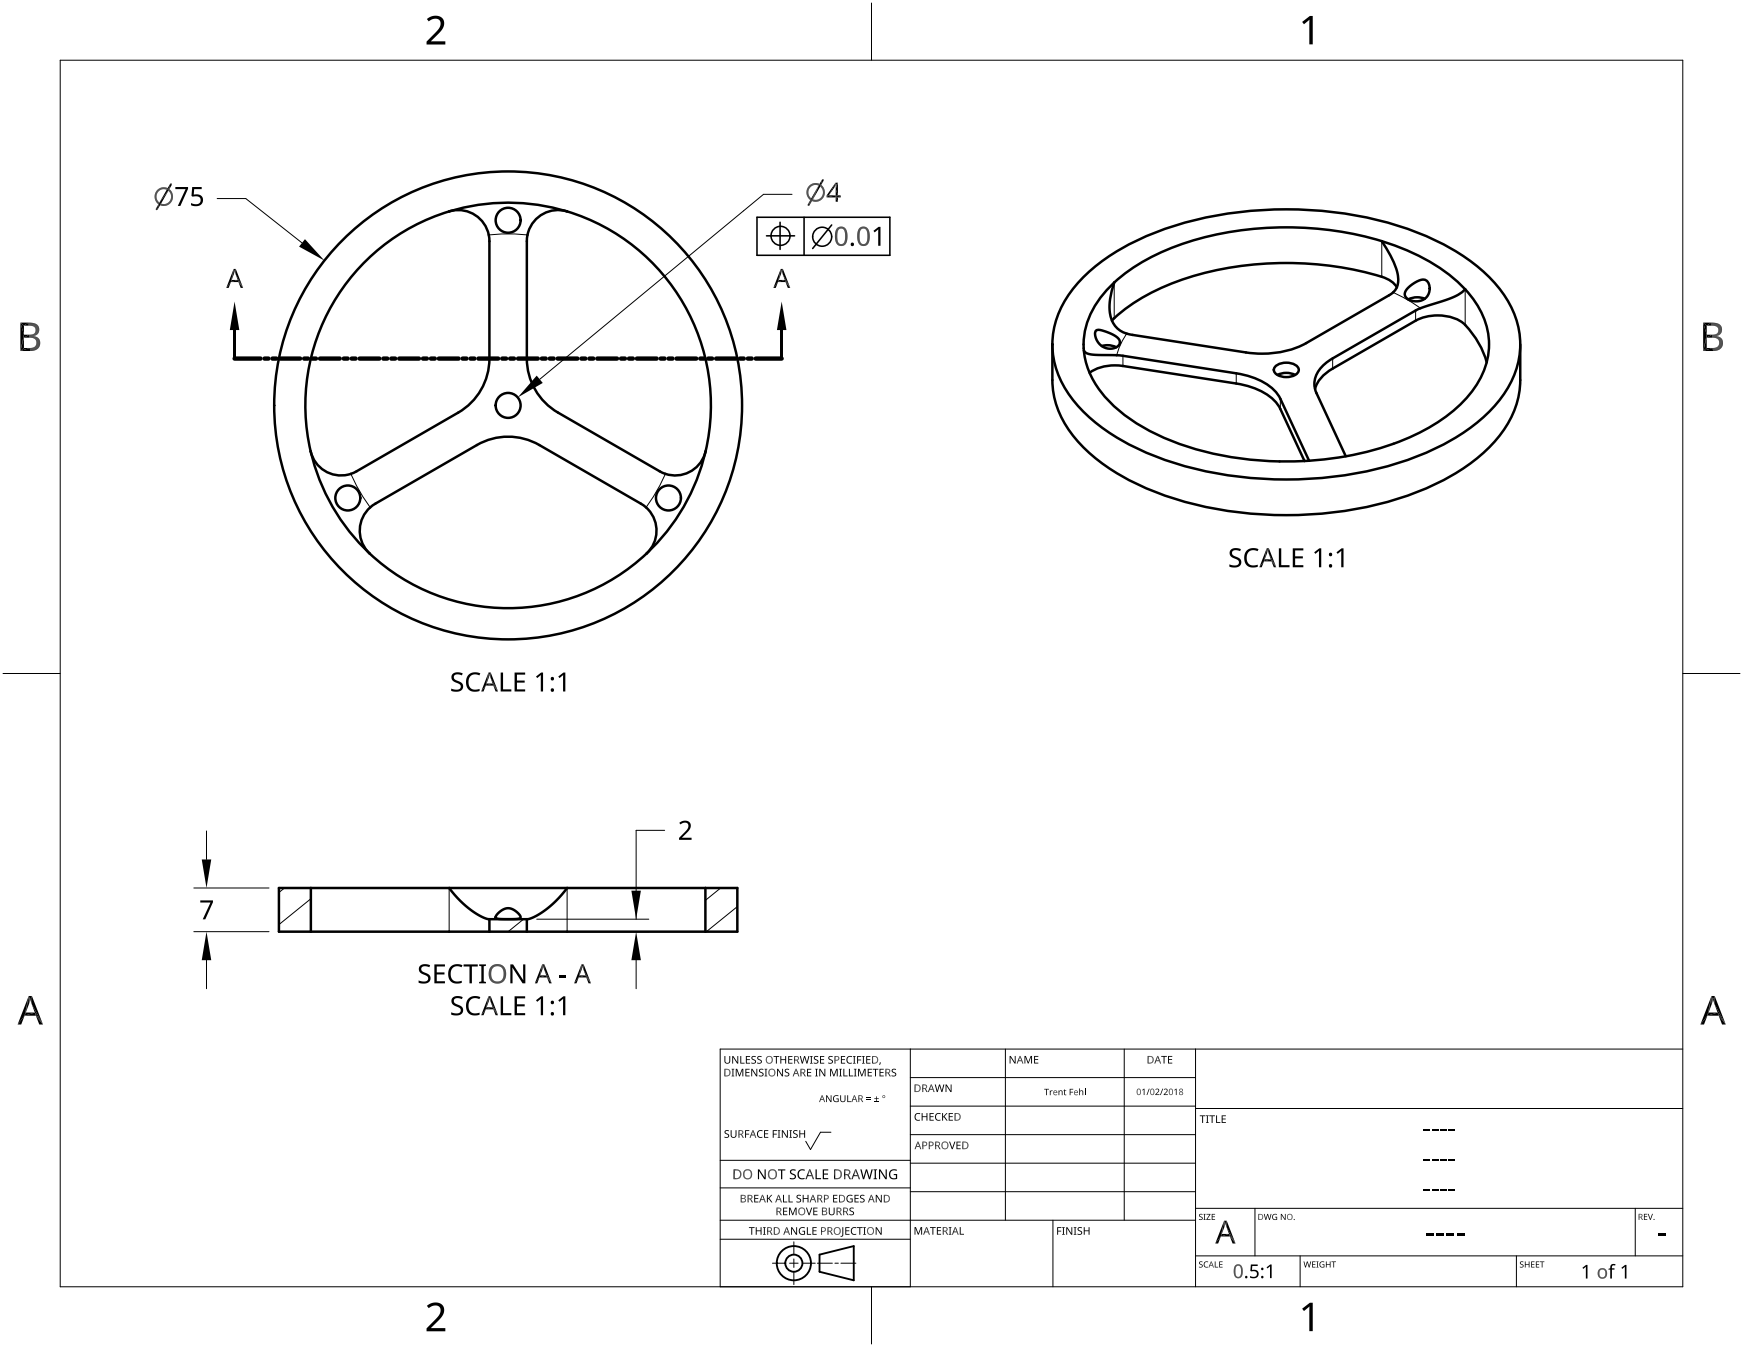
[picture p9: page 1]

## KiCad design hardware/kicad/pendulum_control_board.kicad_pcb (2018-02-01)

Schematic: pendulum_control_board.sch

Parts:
BT1, BT2: 1048; BAT_1048
C1, C4, C5, C7, C8, C10, C11, C12, C13, C14, C15, C16, C18, C19, C20, C21, C22, C23, C25, C26, C37, C41, C43, C47, C56, C64, C65, C66, C71, C72, C74, C75, C79, C82: 0.1uF; SPARKFUN-CAPACITORS_0603
C2, C57, C58, C59, C60, C61, C62, C63, C67, C68, C69, C70: 1.0uF; SPARKFUN-CAPACITORS_0603
C3, C6: 10uF; SPARKFUN-CAPACITORS_0603
C9, C28, C31, C32, C35: 10nF; SPARKFUN-CAPACITORS_0603
C17, C24, C49, C53: 1uF; SPARKFUN-CAPACITORS_0603
C27: 10uF; SPARKFUN-CAPACITORS_0805
C29, C33: 1nF; SPARKFUN-CAPACITORS_0603
C30, C34, C40, C46: 33nF; SPARKFUN-CAPACITORS_0603
C36, C39, C42, C45: 100uF; C_1206
C38, C44: 5.6nF; SPARKFUN-CAPACITORS_0603
C48, C51, C52, C55: 4.7uF; SPARKFUN-CAPACITORS_0603
C50, C54: 47nF; SPARKFUN-CAPACITORS_0603
C73, C76: 1.0uF; SPARKFUN-CAPACITORS_0805
C77: 10uF; SPARKFUN-CAPACITORS_1210
C78: 2.2uF; SPARKFUN-CAPACITORS_0603
C80, C81: 4.7pF; SPARKFUN-CAPACITORS_0603
D1, D17: MBR0520; SOD-123
D2: BAT54C; DIODE_SOT23
D3, D4, D16: 5973311402; SPARKFUN-LED_LED-1206
D5, D6: Yellow; SPARKFUN-LED_LED-0603
D7, D8, D9, D10: 15V; SPARKFUN-DISCRETESEMI_PANASONIC_SMINI2-F5-B
D11, D12, D13, D14: 1N4148; SOD-123
D15: QBLP677-RGB; SPARKFUN-LED_P-LCC-4-3
FB1, FB2, FB3: 30~/1.8A; SPARKFUN-COILS_0603
IC1: STM32F411CEU6; MICRO-STM_V3_UFQFPN48
IC2: LM358D; LINEAR_SO08
J1: DX07S024JJ2; TRISTAN+ROBITAILLE'S+LIBRARY_DX07S0224JJ2_USB-C
L1, L2: MSS1038-153ML; INDUCTOR-COILCRAFT_MSS1038
PAD1: T1-; WIREPAD_1_6_0_8
PAD2: T2-; WIREPAD_1_6_0_8
PAD3: T3-; WIREPAD_1_6_0_8
PAD4: T4-; WIREPAD_1_6_0_8
PAD5: T1+; WIREPAD_1_6_0_8
PAD6: T2+; WIREPAD_1_6_0_8
PAD7: T3+; WIREPAD_1_6_0_8
PAD8: T4+; WIREPAD_1_6_0_8
Q1, Q2, Q3, Q4: BSS138; BSS138_10_SOT23
Q5, Q6, Q7: 2N7002; TRANSISTOR-FET_SOT23
R1: 900K; SPARKFUN-RESISTORS_0603
R2, R5, R6, R9, R50, R63: 4.7K; SPARKFUN-RESISTORS_0603
R3, R4: 200K; SPARKFUN-RESISTORS_0603
R7, R8: 470; SPARKFUN-RESISTORS_0603
R10, R15, R17, R21, R25, R27, R28, R29, R30, R31, R34, R35, R38, R48, R66, R76, R89, R91, R102, R106: 10K; SPARKFUN-RESISTORS_0603
R11, R12, R13, R14, R19, R20, R23, R24: 68; SPARKFUN-RESISTORS_0603
R16, R18, R22, R26, R46, R100, R101: DNP; SPARKFUN-RESISTORS_0603
R32, R33, R36, R37, R51, R59, R64, R67, R70: 1K; SPARKFUN-RESISTORS_0603
R39, R52: 47K; SPARKFUN-RESISTORS_0603
R40, R53: 33K; SPARKFUN-RESISTORS_0603
R41, R54: 100; SPARKFUN-RESISTORS_0603
R42, R55, R61: 1.8K; SPARKFUN-RESISTORS_0603
R43, R56: 5.6K; SPARKFUN-RESISTORS_0603
R44, R57, R93, R94, R95, R96, R105: 100K; SPARKFUN-RESISTORS_0603
R45, R58: 0.3; SPARKFUN-RESISTORS_0603
R47, R65: 187K; SPARKFUN-RESISTORS_0603
R49, R62: 1M; SPARKFUN-RESISTORS_0603
R60, R68: 80; SPARKFUN-RESISTORS_0603
R69, R71, R73: 3K; SPARKFUN-RESISTORS_0603
R72: 140; SPARKFUN-RESISTORS_0603
R74: 4.5K; SPARKFUN-RESISTORS_0603
R75: 4.7; SPARKFUN-RESISTORS_0603
R77, R90, R92: 220; SPARKFUN-RESISTORS_0603
R78: 402K; SPARKFUN-RESISTORS_0603
R79: 107K; SPARKFUN-RESISTORS_0603
R80: SPARKFUN-RESISTORS_0603
R81, R82, R86, R87: 1; SPARKFUN-RESISTORS_0603
R83, R103, R104: 0; SPARKFUN-RESISTORS_0603
R84: 2K; SPARKFUN-RESISTORS_0603
R85: 115K; SPARKFUN-RESISTORS_0603
R88: 0.01; SPARKFUN-RESISTORS_0603
R97: 330; SPARKFUN-RESISTORS_0603
R98: 20; SPARKFUN-RESISTORS_0603
R99: 1m; R_1206
S1, S2: SPARKFUN-SWITCHES_SWITCH_SPST_SMD_A
S3: SW-SPST; SPARKFUN-SWITCHES_TACTILE_SWITCH_SMD_5.2MM
TP1, TP2, TP3, TP4, TP7: TP-040; KEYSTONE_TP-040
TP5, TP6: TP-040; SolderWirePad_single_2mmDrill
U1: FT231XS; SPARKFUN-IC-COMMS_SSOP20_L
U2, U3: V_REG_317SMD; SPARKFUN-IC-POWER_SOT223
U5: LTC6102DD; LINEAR-TECHNOLOGY_DFN8-3X3
U$1, U$7: L6235; L6234_SO24W
U$2, U$11: TPS61175; LIS3DE_HTSSOP14PWP
U$3: LIS3DE; LIS3DE_LGA-16
U$4: L3GD20H; LIS3DE_LGA-16
U$5: AD7280A; LIS3DE_LQFP48_N
U$6: TUSB320LAI; LIS3DE_X2QFN-12
U$8: ITS13FV2SR; LIS3DE_ITS13FV2SR
U$9, U$13: SS3P6L; LIS3DE_TO-277A
U$10: ISL9238; LIS3DE_TQFN-32
U$12: WE-SD; LIS3DE_ROD-CORE-CHOKE
U$14, U$15, U$16, U$17: EPC2023; LIS3DE_EPC2023
U$18: SI7655DN; LIS3DE_POWERPAK-1212-8S
X1, X2: 5566-8; CON-MOLEX_5566-8
Y2: 32.768kHz; SPARKFUN-CLOCKS_CRYSTAL-SMD-3.2X1.5MM

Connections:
/3P3V: C3.2, C4.2, C5.2, C6.2, C8.1, C10.2, C57.1, C72.2, C73.1, D5.A, D6.A, IC1.9 (VDDA), IC1.24 (VDD), IC1.36 (VDD), IC1.48 (VDD), R3.1, R4.2, R5.2, R6.2, R61.2, R72.1, R76.2, R77.2, R89.2, R90.2, R91.2, R92.2, R93.2, R95.2, R106.2, TP5.1, U1.3 (VCCIO), U1.13 (3V3OUT), U2.2 (OUT), U$3.1 (VDD_IO), U$3.14 (VDD), U$4.1 (VDD_IO), U$4.16 (VDD), U$5.29 (VDRIVE), U$6.12 (VDD)
/5V: C2.1, C74.1, IC2.8 (V+), R70.2, TP6.1, U3.2 (OUT), U5.3 (V-/EN), U5.7 (V+), X1.3, X2.3
/ACOK: Q5.1 (G), R76.1, U$10.24 (ACOK)
/ALERT_BATT: IC1.40 (PB4), U$5.27 (ALERT)
/AUX_TERM: R102.2, U$5.32 (AUX_TERM)
/BATGONE: S2.2, U$10.25 (BATGONE)
/BOOT0: IC1.44 (BOOT0), R105.2, TP7.1
/BRAKE_X: IC1.45 (PB8), U$1.14 (BRAKE)
/BRAKE_Y: IC1.12 (PA2), U$7.14 (BRAKE)
/CB1: R15.1, U$5.12 (CB1)
/CB2: R17.1, U$5.10 (CB2)
/CB3: R21.1, U$5.8 (CB3)
/CB4: R25.1, U$5.6 (CB4)
/CC1: J1.A5 (CC1), U$6.1 (CC1)
/CC2: J1.B5 (CC2), U$6.2 (CC2)
/CLK: IC1.25 (PB12), U$3.4 (SCL/SPC), U$4.2 (SCL/SPC), U$5.22 (SCLK)
/CREF: C25.1, U$5.39 (CREF)
/CSON: C68.2, C69.1, R87.1, U$10.1 (CSON)
/CSOP: C68.1, C70.1, R86.1, U$10.2 (CSOP)
/CS_ACCEL: IC1.15 (PA5), U$3.8 (CS)
/CS_BATT: IC1.29 (PA8), U$5.21 (CS)
/CS_GYRO: IC1.21 (PB10), U$4.5 (CS)
/DEN_GYRO: IC1.18 (PB0), U$4.8 (DEN)
/DM: J1.A7 (D-), J1.B7 (D-), U1.12 (USBDM)
/DP: J1.A6 (D+), J1.B6 (D+), U1.11 (USBDP)
/DRDY/INT2_GYRO: IC1.20 (PB2), U$4.6 (DRDY/INT2)
/EN_BLU_L: D15.3 (BLU), IC1.34 (PA13)
/EN_GRN_L: D15.2 (GRN), IC1.37 (PA14)
/EN_RED_H: IC1.38 (PA15), R74.1
/EN_RED_L: IC1.39 (PB3), R73.2
/EN_WHEEL: IC1.10 (PA0-WKUP), R44.2, R57.2
/FWD/REV_X: IC1.46 (PB9), U$1.11 (FWD/REV)
/FWD/REV_Y: IC1.11 (PA1), U$7.11 (FWD/REV)
/HALL1_X: U$1.1 (H1), X1.1
/HALL1_Y: U$7.1 (H1), X2.1
/HALL2_X: U$1.23 (H2), X1.2
/HALL2_Y: U$7.23 (H2), X2.2
/HALL3_X: U$1.24 (H3), X1.5
/HALL3_Y: U$7.24 (H3), X2.5
/INT1_ACCEL: IC1.13 (PA3), U$3.11 (INT1)
/INT1_GRYO: IC1.19 (PB1), U$4.7 (INT1)
/INT2_ACCEL: IC1.14 (PA4), U$3.9 (INT2)
/I_BATT: IC1.3 (PC14), R100.2, U5.4 (OUT)
/MISO: IC1.16 (PA6), U$3.7 (SDO/SA0), U$4.4 (SDO/SA0), U$5.26 (SDO)
/MOSI: IC1.17 (PA7), U$3.6 (SDO/SDI/SDA), U$4.3 (SDA/SDI/SDO), U$5.23 (SDI)
/N$1: R2.1, U$6.3 (PORT)
/N$2: R8.1, U1.10 (CBUS2)
/N$3: R4.1, U$6.6 (INT_N/OUT3)
/N$4: D5.C, R8.2
/N$5: R7.1, U1.17 (CBUS1)
/N$6: R1.2, U$6.4 (VBUS_DET)
/N$7: D6.C, R7.2
/N$8: C9.2, U$4.14 (CAP)
/N$9: D7.C, Q1.1 (G), R15.2, R16.2
/N$10: R9.1, R10.2, U1.19 (CBUS3)
/N$11: R3.2, U$6.9 (ID)
/N$12: D8.C, Q2.1 (G), R17.2, R18.2
/N$13: C11.1, C12.2, C19.1, R28.2, U$5.11 (VIN1)
/N$14: C7.1, U1.14 (~RESET)
/N$15: Q1.3 (D), R13.1, R14.1
/N$16: C33.1, R40.2, U$1.4 (RCOFF)
/N$17: C78.1, IC1.22 (VCAP1)
/N$18: IC1.6 (OSC_OUT), R103.1
/N$19: R38.2, U$5.14 (MASTER)
/N$20: Q2.3 (D), R11.1, R12.1
/N$21: D9.C, Q3.1 (G), R21.2, R22.2
/N$22: Q3.3 (D), R19.1, R20.1
/N$23: D10.C, Q4.1 (G), R25.2, R26.2
/N$24: Q4.3 (D), R23.1, R24.1
/N$25: C31.2, R39.2, U$1.9 (RCPULSE)
/N$26: C29.1, R53.2, U$7.4 (RCOFF)
/N$27: R37.2, U$5.25 (SDO_IO)
/N$28: C13.1, C14.2, C20.1, R30.2, U$5.7 (VIN3)
/N$29: C11.2, C18.1, R27.2, U$5.13 (VIN0)
/N$30: C14.1, C22.1, R31.2, U$5.5 (VIN4)
/N$31: C12.1, C13.2, C21.1, R29.2, U$5.9 (VIN2)
/N$32: R33.2, U$5.43 (SDI_HI)
/N$33: R32.2, U$5.42 (ALERT_HI)
/N$34: R36.2, U$5.28 (ALERT_IO)
/N$35: C28.2, R52.2, U$7.9 (RCPULSE)
/N$36: R35.1, U$5.34 (AUX5)
/N$37: R34.1, U$5.33 (AUX6)
/N$38: C38.1, R44.1, U$1.2 (DIAG), U$1.12 (EN)
/N$39: C40.2, IC2.2 (-IN), R49.2, R50.1
/N$40: C44.1, R57.1, U$7.2 (DIAG), U$7.12 (EN)
/N$41: R51.2, R64.2
/N$42: C40.1, IC2.1 (OUT), R43.2, R49.1
/N$43: R58.1, U$7.3 (SENSEA), U$7.10 (SENSEB)
/N$44: R45.1, U$1.3 (SENSEA), U$1.10 (SENSEB)
/N$45: C45.1, D13.1 (K), U$7.15 (VBOOT)
/N$47: C39.1, D11.1 (K), U$1.15 (VBOOT)
/N$49: C35.1, R41.1
/N$50: C35.2, U$1.22 (VCP)
/N$51: C32.1, R54.1
/N$52: C32.2, U$7.22 (VCP)
/N$53: L1.2, U$2.1 (SW), U$2.2 (SW), U$9.PIN1 (A), U$9.PIN2 (A)
/N$54: C53.2, U$11.8 (COMP)
/N$55: R60.2, U$11.10 (FREQ)
/N$56: C46.2, IC2.6 (-IN), R62.2, R63.1
/N$57: C54.1, U$11.5 (SS)
/N$58: C53.1, R59.2
/N$59: R47.1, R48.2, U$11.9 (FB)
/N$60: L2.2, U$11.1 (SW), U$11.2 (SW), U$13.PIN1 (A), U$13.PIN2 (A)
/N$61: C46.1, IC2.7 (OUT), R56.2, R62.1
/N$62: C62.2, D1.1 (K), U$10.10 (PHASE1), U$10.12 (BOOT1), U$12.P$1 (1), U$14.2 (S), U$14.5 (S), U$14.6 (S), U$14.9 (S), U$14.10 (S), U$14.13 (S), U$14.14 (S), U$14.17 (S), U$14.18 (S), U$14.21 (S), U$14.22 (S), U$14.25 (S), U$14.26 (S), U$14.29 (S), U$15.3 (D), U$15.4 (D), U$15.7 (D), U$15.8 (D), U$15.11 (D), U$15.12 (D), U$15.15 (D), U$15.16 (D), U$15.19 (D), U$15.20 (D), U$15.23 (D), U$15.24 (D), U$15.27 (D), U$15.28 (D)
/N$63: D15.4 (A), R72.2
/N$64: R70.1, R71.2, U3.1 (ADJ)
/N$65: C63.1, D17.1 (K), U$10.4 (BOOT2), U$10.6 (PHASE2), U$12.P$2 (4), U$16.2 (S), U$16.5 (S), U$16.6 (S), U$16.9 (S), U$16.10 (S), U$16.13 (S), U$16.14 (S), U$16.17 (S), U$16.18 (S), U$16.21 (S), U$16.22 (S), U$16.25 (S), U$16.26 (S), U$16.29 (S), U$17.3 (D), U$17.4 (D), U$17.7 (D), U$17.8 (D), U$17.11 (D), U$17.12 (D), U$17.15 (D), U$17.16 (D), U$17.19 (D), U$17.20 (D), U$17.23 (D), U$17.24 (D), U$17.27 (D), U$17.28 (D)
/N$66: C49.2, U$2.8 (COMP)
/N$67: R68.2, U$2.10 (FREQ)
/N$68: C50.1, U$2.5 (SS)
/N$69: C49.1, R67.2
/N$70: R61.1, R69.2, U2.1 (ADJ)
/N$71: R65.1, R66.2, U$2.9 (FB)
/N$72: C67.1, R84.2
/N$73: R83.2, U$10.29 (AMON/BMON)
/N$74: D15.1 (RED), R73.1, R74.2
/N$75: IC1.5 (OSC_IN), R104.1
/N$76: C80.1, R103.2, Y2.P$2 (2)
/N$77: C81.2, R104.2, Y2.P$1 (1)
/N$79: C59.1, R75.1, U$10.18 (VDD)
/N$80: D3.C, Q5.3 (D)
/N$81: C58.1, R83.1
/N$82: D3.A, R77.1
/N$83: U$10.32 (BGATE), U$18.4 (G)
/N$85: R98.2, U5.1 (-INS), U5.2 (-INF)
/N$86: R93.1, S2.3 (S)
/N$87: R94.2, S2.1 (O)
/N$88: D4.C, Q6.3 (D)
/N$89: D4.A, R90.1
/N$91: C64.1, C65.1, R82.2, U$10.14 (CSIN)
/N$92: C64.2, C66.2, R81.2, U$10.15 (CSIP)
/N$94: R80.1, R82.1, TP4.1, U$14.3 (D), U$14.4 (D), U$14.7 (D), U$14.8 (D), U$14.11 (D), U$14.12 (D), U$14.15 (D), U$14.16 (D), U$14.19 (D), U$14.20 (D), U$14.23 (D), U$14.24 (D), U$14.27 (D), U$14.28 (D)
/N$95: D16.C, Q7.3 (D)
/N$96: D16.A, R92.1
/N$98: R95.1, S1.3 (S)
/N$99: C61.2, R78.1, R79.2, U$10.19 (ACIN)
/N$100: R96.2, S1.1 (O)
/N$101: R97.1, U$8.L2
/N$107: D2.3 (CC), U$10.17 (DCIN)
/N$108: R84.1, U$10.28 (COMP)
/N$109: U$10.9 (LGATE1), U$15.1 (G)
/N$110: R85.1, U$10.27 (PROG)
/N$111: U$10.11 (UGATE1), U$14.1 (G)
/N$116: C74.2, U5.6 (VREG)
/N$117: U$10.7 (LGATE2), U$17.1 (G)
/N$118: U$10.5 (UGATE2), U$16.1 (G)
/OTGEN/CMIN: S1.2, U$10.20 (OTGEN/CMIN)
/OTGPG/CMOUT: Q7.1 (G), R91.1, U$10.26 (OTGPG/CMOUT)
/OUT1_X: U$1.5 (OUT1), X1.7
/OUT1_Y: U$7.5 (OUT1), X2.7
/OUT2_X: U$1.21 (OUT2), X1.8
/OUT2_Y: U$7.21 (OUT2), X2.8
/OUT3_X: U$1.16 (OUT3), X1.4
/OUT3_Y: U$7.16 (OUT3), X2.4
/PD_BATT: IC1.41 (PB5), U$5.15 (PD)
/PROCHOT: Q6.1 (G), R89.1, U$10.23 (PROCHOT)
/PSYS: IC1.2 (PC13), U$10.30 (PSYS)
/RST: C71.1, C82.2, IC1.7 (NRST), S3.1, S3.2 (1)
/SCL: IC1.42 (PB6), R6.1, U$6.8 (SCL/OUT2), U$10.22 (SCL)
/SDA: IC1.43 (PB7), R5.1, U$6.7 (SDA/OUT1), U$10.21 (SDA)
/SW1: C79.2, IC1.27 (PB14), R106.1, U$8.1, U$8.2
/SW_LED_GH_RL: IC1.26 (PB13), U$8.L1
/SW_LED_RH_GL: IC1.28 (PB15), R97.2
/TACHO_X: R50.2, R51.1, U$1.8 (TACHO)
/TACHO_Y: R63.2, R64.1, U$7.8 (TACHO)
/T_CELL1: PAD5.1, U$5.38 (AUX1)
/T_CELL2: PAD6.1, U$5.37 (AUX2)
/T_CELL3: PAD7.1, U$5.36 (AUX3)
/T_CELL4: PAD8.1, U$5.35 (AUX4)
/UART_CTS: IC1.32 (PA11), U1.9 (~CTS)
/UART_RTS: IC1.33 (PA12), U1.2 (~RTS)
/UART_RXD: IC1.31 (PA10), U1.20 (TXD)
/UART_TXD: IC1.30 (PA9), U1.4 (RXD)
/VDDP: C60.1, R75.2, U$10.8 (VDDP)
/VDD_BATT: C15.1, C27.1, FB1.1, R32.1, R33.1, R38.1, U$5.16 (VDD), U$5.44 (CNVST_HI), U$5.45 (SDO_HI), U$5.46 (SCLK_HI), U$5.47 (CS_HI), U$5.48 (PD_HI)
/VREF: C24.1, C41.1, C47.1, IC2.3 (+IN), IC2.5 (+IN), U$5.40 (VREF)
/VREF_X: C34.2, R42.2, R43.1, U$1.13 (VREF)
/VREF_Y: C30.2, R55.2, R56.1, U$7.13 (VREF)
/VSYS+: C75.1, C76.1, C77.1, D2.2 (A2), R86.2, R88.2, TP1.1, U$10.3 (VSYS), U$16.3 (D), U$16.4 (D), U$16.7 (D), U$16.8 (D), U$16.11 (D), U$16.12 (D), U$16.15 (D), U$16.16 (D), U$16.19 (D), U$16.20 (D), U$16.23 (D), U$16.24 (D), U$16.27 (D), U$16.28 (D)
/VSYS-: R87.2, R88.1, TP2.1, U$18.1 (S), U$18.2 (S), U$18.3 (S)
/V_BATT: C1.2, C48.2, C52.2, C56.2, L1.1, L2.1, R98.1, R99.2, U2.3 (IN), U3.3 (IN), U$2.3 (VIN), U$2.4 (EN), U$10.31 (VBAT), U$11.3 (VIN), U$11.4 (EN), U$18.5 (D), U$18.6 (D), U$18.7 (D), U$18.8 (D), U$18.P (D)
/V_BUS: D2.1 (A1), J1.A4 (V+), J1.A9 (V+), J1.B4 (V+), J1.B9 (V+), R1.1, R9.2, R78.2, R80.2, R81.1, TP3.1, U1.15 (VCC), U$10.16 (ADP)
/V_CELL1: BT1.C1-, BT1.C2+, D8.A, IC1.1 (VBAT), Q2.2 (S), R13.2, R14.2, R18.1, R28.1
/V_CELL2: BT1.C1+, BT2.C2-, D9.A, Q3.2 (S), R11.2, R12.2, R22.1, R29.1
/V_CELL3: BT2.C1-, BT2.C2+, D10.A, Q4.2 (S), R19.2, R20.2, R26.1, R30.1
/V_CELL4: BT2.C1+, C26.1, FB1.2, R23.2, R24.2, R31.1, R99.1, U5.8 (+IN)
/V_DRIVER_X: C36.2, C37.2, C39.2, C51.1, D12.2 (A), R65.2, U$1.17 (VSB), U$1.20 (VSA), U$9.PIN3 (C)
/V_DRIVER_Y: C42.2, C43.2, C45.2, C55.1, D14.2 (A), R47.2, U$7.17 (VSB), U$7.20 (VSA), U$13.PIN3 (C)
/V_REG_BATT: C16.1, C17.1, C23.1, PAD1.1, PAD2.1, PAD3.1, PAD4.1, R34.2, R35.2, U$5.18 (VREG), U$5.19 (DVCC), U$5.24 (CNVST), U$5.30 (AVCC)
GND: BT1.C2-, C1.1, C2.2, C3.1, C4.1, C5.1, C6.1, C7.2, C8.2, C9.1, C10.1, C15.2, C16.2, C17.2, C18.2, C19.2, C20.2, C21.2, C22.2, C23.2, C24.2, C25.2, C26.2, C27.2, C28.1, C29.2, C30.1, C31.1, C33.2, C34.1, C36.1, C37.1, C38.2, C41.2, C42.1, C43.1, C44.2, C47.2, C50.2, C54.2, C56.1, C57.2, C58.2, C59.2, C60.2, C61.1, C62.1, C63.2, C65.2, C66.1, C67.2, C69.2, C70.2, C71.2, C72.1, C73.2, C75.2, C76.2, C77.2, C78.2, C79.1, C80.2, C81.1, C82.1, D1.2 (A), D7.A, D17.2 (A), FB2.2, FB3.2, IC1.8 (VSSA), IC1.23 (VSS), IC1.35 (VSS), IC1.47 (VSS), IC2.4 (V-), J1.A1 (GND), J1.A12 (GND), J1.B1 (GND), J1.B12 (GND), J1.SHIE (SHIELD), Q1.2 (S), Q5.2 (S), Q6.2 (S), Q7.2 (S), R2.2, R10.1, R16.1, R27.1, R36.1, R37.1, R39.1, R40.1, R42.1, R45.2, R46.1, R48.1, R52.1, R53.1, R55.1, R58.2, R59.1, R60.1, R66.1, R67.1, R68.1, R69.1, R71.1, R79.1, R85.2, R94.1, R96.1, R100.1, R101.1, R102.1, R105.1, S3.3 (2), S3.4 (2), U1.6 (GND), U1.16 (GND), U5.5 (V-), U$1.6 (GND), U$1.7 (GND), U$1.18 (GND), U$1.19 (GND), U$2.6 (SYNC), U$2.7 (AGND), U$2.11 (NC), U$3.5 (GND), U$3.10 (RES), U$3.12 (GND), U$4.9 (RES), U$4.10 (RES), U$4.11 (RES), U$4.12 (GND), U$4.13 (GND), U$4.15 (RES), U$5.17 (VSS), U$5.20 (DGND), U$5.31 (AGND), U$5.41 (REFGND), U$6.5 (ADDR), U$6.10 (GND), U$6.11 (EN_N), U$7.6 (GND), U$7.7 (GND), U$7.18 (GND), U$7.19 (GND), U$8.3, U$8.4, U$10.GND, U$11.6 (SYNC), U$11.7 (AGND), U$11.11 (NC), U$15.2 (S), U$15.5 (S), U$15.6 (S), U$15.9 (S), U$15.10 (S), U$15.13 (S), U$15.14 (S), U$15.17 (S), U$15.18 (S), U$15.21 (S), U$15.22 (S), U$15.25 (S), U$15.26 (S), U$15.29 (S), U$17.2 (S), U$17.5 (S), U$17.6 (S), U$17.9 (S), U$17.10 (S), U$17.13 (S), U$17.14 (S), U$17.17 (S), U$17.18 (S), U$17.21 (S), U$17.22 (S), U$17.25 (S), U$17.26 (S), U$17.29 (S), X1.6, X2.6
GNDPWR: C48.1, C51.2, C52.1, C55.2, FB2.1, FB3.1, R46.2, R101.2, U$2.12 (PGND), U$2.13 (PGND), U$2.14 (PGND), U$2.EXP (PGND), U$11.12 (PGND), U$11.13 (PGND), U$11.14 (PGND), U$11.EXP (PGND)
unnamed: D11.2 (A), D12.1 (K), R41.2
unnamed: D13.2 (A), D14.1 (K), R54.2

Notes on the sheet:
REV2: Replace with USART part
NOTE: 80 Ohm resistor sets FREQ to 1200 kHz, 187 KOhm sets V_DRIVER close to 24 V
QUESTION: Do I need DTR, DSR, DCR, and RI connected to the micro?
#TODO: Get resistor values double checked
NOTE: Max Vf for RED is 2.5 V
NOTE: Is this okay to interface with the 3.3V micro?
NOTE: Battery cells are INR18650-25R
Motor Drive
Battery Charging and Monitoring
Sensing
NOTE: C78 needs to be low ESR
NOTE: Motors are Maxon EC 45 flat 70 Watt (PN: 397172)

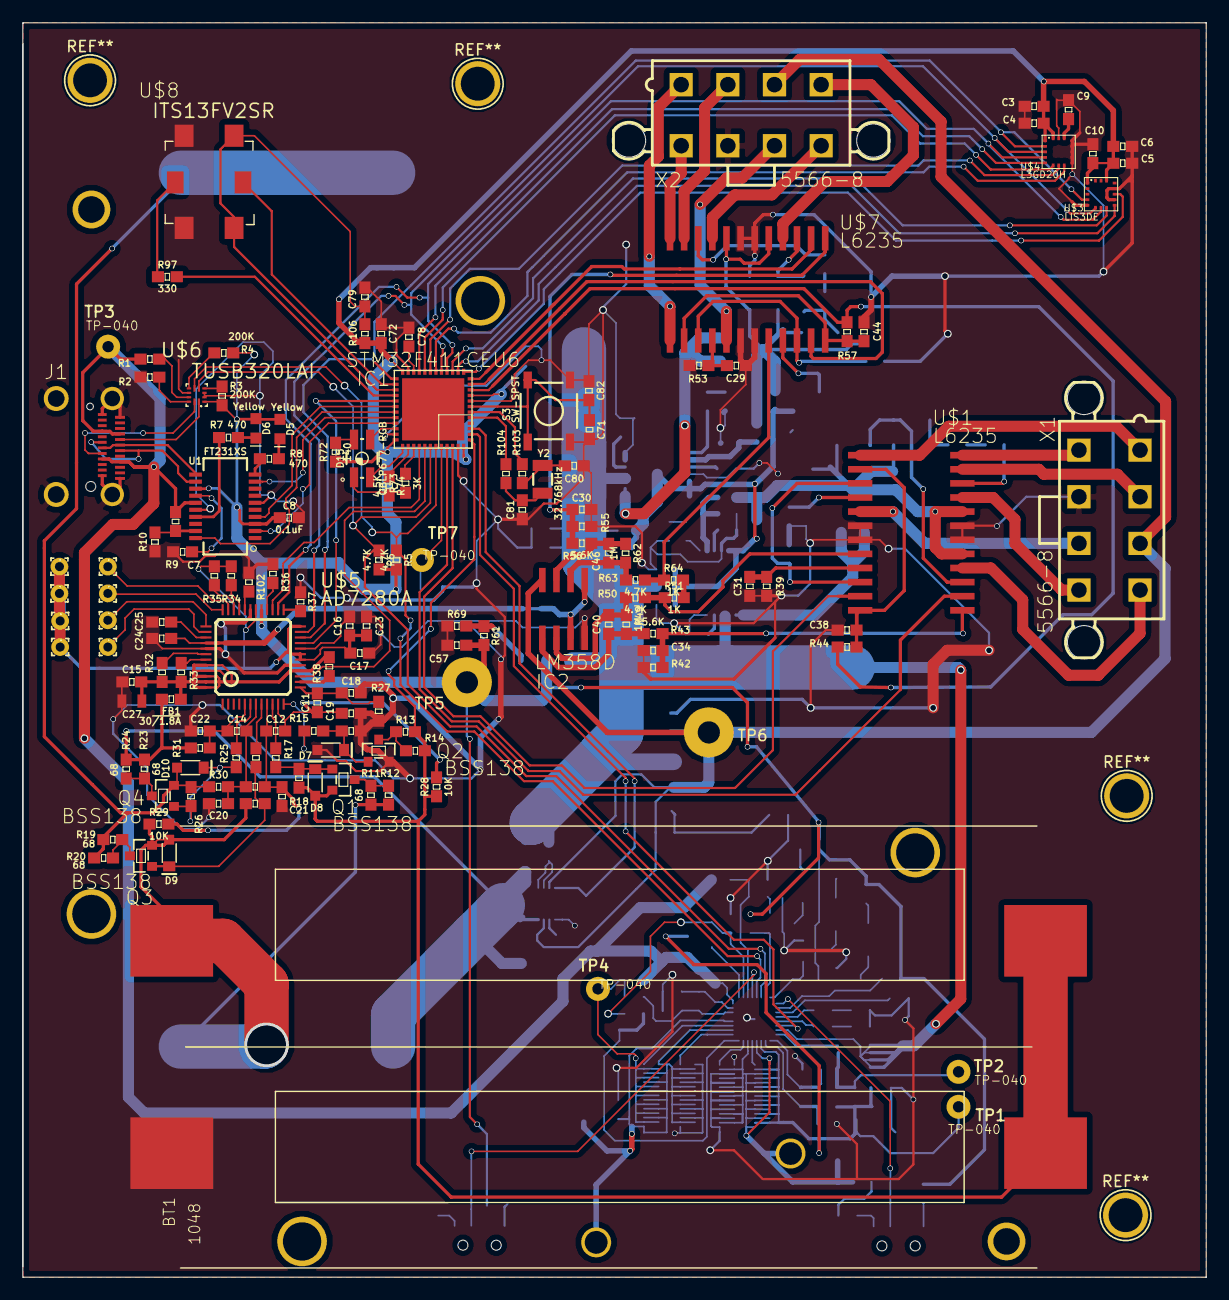
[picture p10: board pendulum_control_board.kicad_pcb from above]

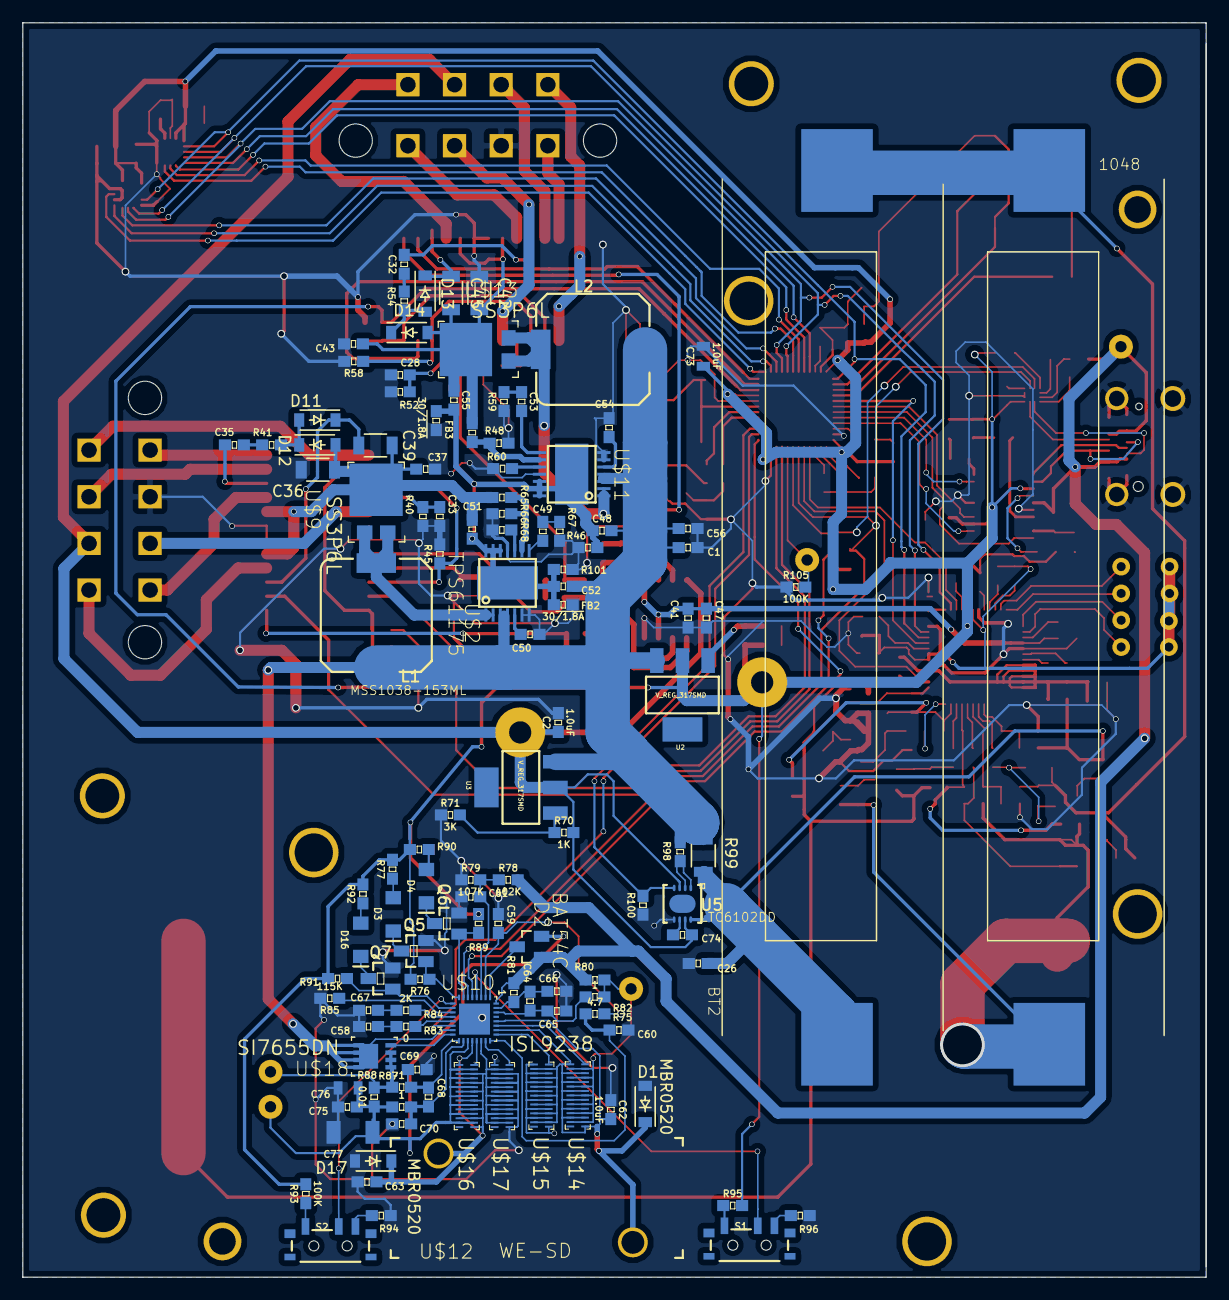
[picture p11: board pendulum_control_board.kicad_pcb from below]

Board: 2 copper layers, 106.5 x 112.9 mm, 265 parts (120 on the bottom side), 194 nets.

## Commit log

2017-12-31 added wheel part
    [wheel.stl]
2017-12-31 added step version of part
    [wheel.step]
2018-01-06 added cad file
    [wheel.step, wheel.stl]
2018-01-06 adding kicad
    [pendulum_control_board.kicad_pcb, pendulum_control_board.sch, wheel.step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]
2018-01-06 removed duplicated files
    [wheel.step, wheel.stl]
2018-01-06 removed kicad default library from this repo
2018-01-06 adding wheel drawing
2018-01-07 adding wheel cad and gcode files
    [wheel.fcstd, wheel.step]
2018-01-15 added bom csv
    [electronics_bom.csv]
2018-01-15 updated PCB and created schematic pdf
    [pendulum_control_board.kicad_pcb]
2018-01-21 added schottkys to charging circuit
    [pendulum_control_board.kicad_pcb, pendulum_control_board.sch]
2018-01-25 added gerber and drill files
    [pendulum_control_board-B.Cu.gbr, pendulum_control_board-B.Mask.gbr, pendulum_control_board-B.SilkS.gbr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]
2018-01-27 added bom and updated board
    [pendulum_control_board.kicad_pcb, pendulum_control_board.sch, pendulum_control_board_bom.csv]
2018-02-01 moved interfering resistor
    [pendulum_control_board.kicad_pcb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]
2018-07-12 got write up to a deceent state
    [pendulum_control_board_bom.xlsx]
